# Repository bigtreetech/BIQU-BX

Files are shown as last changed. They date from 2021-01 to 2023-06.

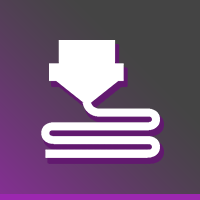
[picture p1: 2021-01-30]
Firmware/Copy to microSD to update/TFT70/bmp/print.bmp

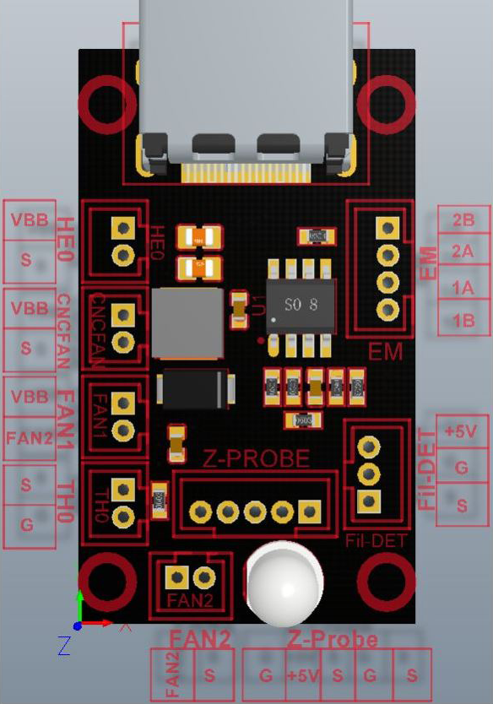
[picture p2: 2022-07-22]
Hardware/BTT BX HotMode V2.0.png

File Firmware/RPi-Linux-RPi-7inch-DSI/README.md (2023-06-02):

# RPi-7inch-DSI

## Support OS

| Hardware | 32-bit | 64-bit |
|  :---: | :---: | :---: |
|  RPi-3 | 6.1.21 |  6.1.21 |
|  RPi-4 | 6.1.21 | 6.1.21 |

## Start installation
1. Download driver from Git
    ``` bash
    git clone --depth=1 -b RPI-DSI-BXV3 https://github.com/bigtreetech/BIQU-BX.git RPI-DSI-BXV3
    ```
    
2. Install the driver
    ``` bash
    cd RPI-DSI-BXV3
    sudo ./install.sh
    ```

3. Wait for the system to restart, and then the display and touch will work normally.

> NOTE: 
> * The above steps need to ensure that the raspberry pi can be connected to the Internet normally.
> * When raspberry pi was started, the display of uboot was still 800*480 resolution, so the display was still abnormal when it was just started. The DSI output would not be normal until the system was running normally
> * Different hardware and kernel versions correspond to different drivers.

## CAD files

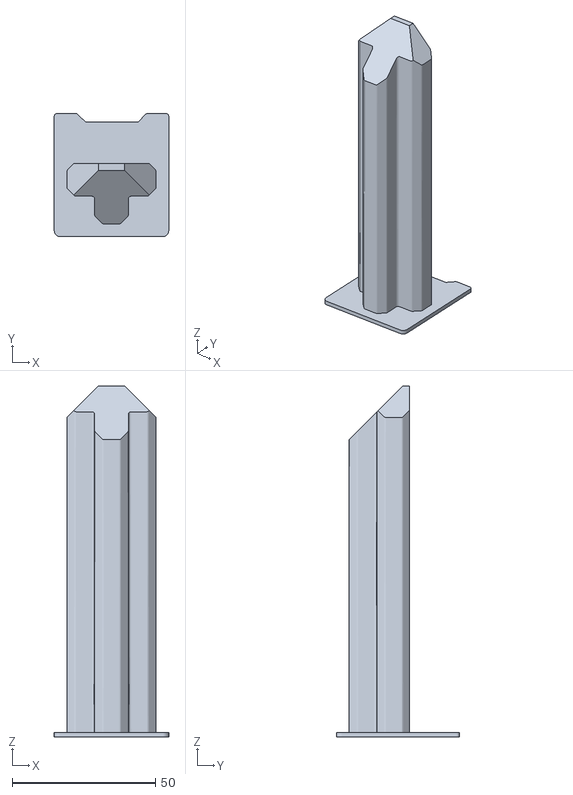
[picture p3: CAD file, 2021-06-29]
TF card data/Models/Drawer.stl
40.0 x 43.0 x 122.6

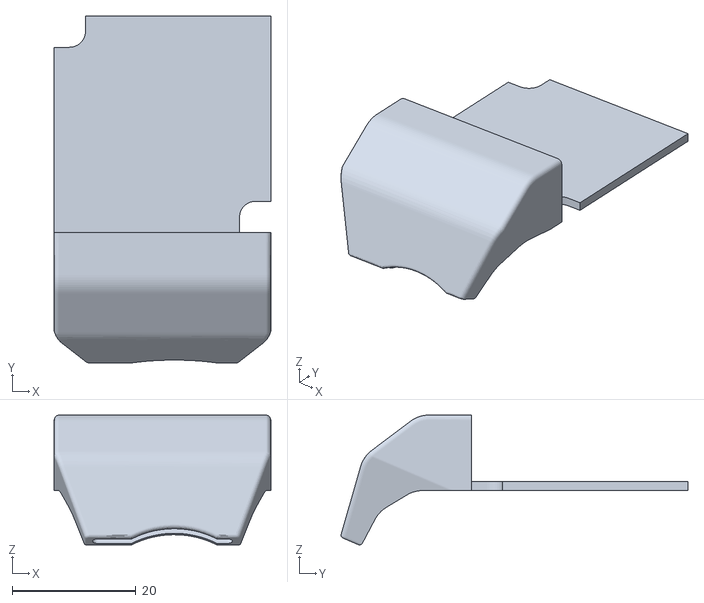
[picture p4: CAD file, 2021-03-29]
TF card data/Models/Parts-Cooling-Fan.stl
35.0 x 56.1 x 21.0

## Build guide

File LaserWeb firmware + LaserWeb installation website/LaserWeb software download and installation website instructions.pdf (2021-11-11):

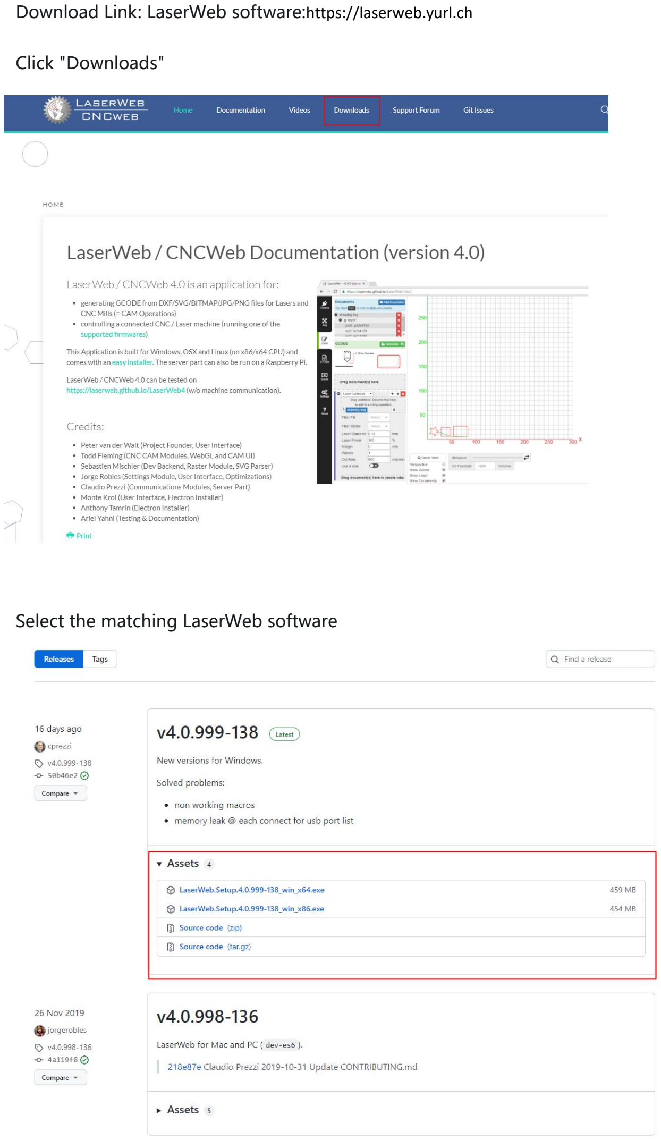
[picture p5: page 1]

Download Link: LaserWeb software:https://laserweb.yurl.ch

Click "Downloads"

Select the matching LaserWeb software

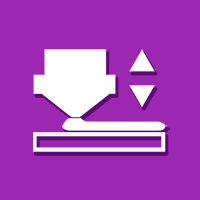
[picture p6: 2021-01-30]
Firmware/Copy to microSD to update/TFT70/bmp/BabyStep.bmp

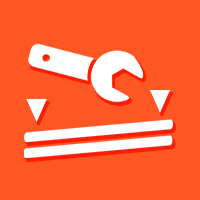
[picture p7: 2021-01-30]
Firmware/Copy to microSD to update/TFT70/bmp/manual_level.bmp

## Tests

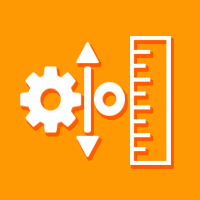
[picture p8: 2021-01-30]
Firmware/Copy to microSD to update/TFT70/bmp/tune_extruder.bmp

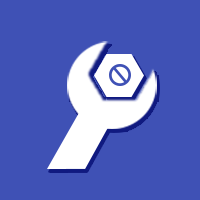
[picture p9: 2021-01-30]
Firmware/Copy to microSD to update/TFT70/bmp/tuning.bmp

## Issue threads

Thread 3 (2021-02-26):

Issues with ABL

KillerOfPie, 2021-02-26:
I just received and setup my BX yesterday and whenever I try to run the ABL it fails. The light on the sensor lights up when it approaches the sheet but the print says it fails significantly above the bed and the z endstop.

Wasn't sure if this is the proper place to report this, if not please let me know where.

KillerOfPie, 2021-02-26:
Once I removed the SD card that came with the printer the ABL worked and everything was fine after putting the card back in.

Closed 2021-02-26.

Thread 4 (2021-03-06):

Unable to Recompile Firmware

dastolly, 2021-03-06:
Cannot compile firmware with a successful flash, even without making any changes to the downloaded files.  Using VS.  I'm trying to get the USB on the TFT to be the connection to Octoprint, as well as enable safe home, but I cannot make these changes and have the printer successfully load the new firmware.  It runs the process up to 100%, but never boots, just stays at a black screen.

inismor, 2021-03-09:
> Cannot compile firmware with a successful flash, even without making any changes to the downloaded files. Using VS. I'm trying to get the USB on the TFT to be the connection to Octoprint, as well as enable safe home, but I cannot make these changes and have the printer successfully load the new firmware. It runs the process up to 100%, but never boots, just stays at a black screen.

Are you compiling BTT_SKR_SE_BX_BOOT? (Not BTT_SKR_SE_BX). Worked for me.

dastolly, 2021-03-11:
> > Cannot compile firmware with a successful flash, even without making any changes to the downloaded files. Using VS. I'm trying to get the USB on the TFT to be the connection to Octoprint, as well as enable safe home, but I cannot make these changes and have the printer successfully load the new firmware. It runs the process up to 100%, but never boots, just stays at a black screen.
>
> Are you compiling BTT_SKR_SE_BX_BOOT? (Not BTT_SKR_SE_BX). Worked for me.

I'm compiling in Visual Studio and I can open 3 folders from the downloaded code.  One folder says "BIQU-BX", one says "BIQU-BX-1", and one says "BIQU-BX-master".  All three folders have similar innards, and all reside inside a "BIQU-BX-master" folder.  No matter which one I select, when I build, the marline auto build shows BTT_SKR_SE_BX.  How can I get to the boot one?

inismor, 2021-03-11:
What you describe isn’t what I saw, and I just downloaded the sources a couple of days ago. PlatformIO only shows BTT_SKR_SE_BX and BTT_SKR_SE_BX_BOOT. Build the _BOOT version and copy the resulting firmware.bin file to an SD card. First time you flash the printer, be sure to add the “config.ini" file and “BTT70" folder from the top-level "Copy to microSD to update” folder. BTT has made some changes to the UI since they shipped.

—r

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

dastolly, 2021-03-11:
> What you describe isn’t what I saw, and I just downloaded the sources a couple of days ago. PlatformIO only shows BTT_SKR_SE_BX and BTT_SKR_SE_BX_BOOT. Build the _BOOT version and copy the resulting firmware.bin file to an SD card. First time you flash the printer, be sure to add the “config.ini" file and “BTT70" folder from the top-level "Copy to microSD to update” folder. BTT has made some changes to the UI since they shipped. —r
> […](#)
> On Mar 10, 2021, 7:20 PM -0500, dastolly ***@***.***>, wrote: > > Cannot compile firmware with a successful flash, even without making any changes to the downloaded files. Using VS. I'm trying to get the USB on the TFT to be the connection to Octoprint, as well as enable safe home, but I cannot make these changes and have the printer successfully load the new firmware. It runs the process up to 100%, but never boots, just stays at a black screen. > Are you compiling BTT_SKR_SE_BX_BOOT? (Not BTT_SKR_SE_BX). Worked for me. I'm compiling in Visual Studio and I can open 3 folders from the downloaded code. One folder says "BIQU-BX", one says "BIQU-BX-1", and one says "BIQU-BX-master". All three folders have similar innards, and all reside inside a "BIQU-BX-master" folder. No matter which one I select, when I build, the marline auto build shows BTT_SKR_SE_BX. How can I get to the boot one? — You are receiving this because you commented. Reply to this email directly, view it on GitHub, or unsubscribe.

I'll give it a shot again, thanks!  I'm just not seeing where to choose between the two.  I'll keep digging.

inismor, 2021-03-11:
You build with PlatformIO, right? Not the compile button.

dastolly, 2021-03-11:
In Visual?  I've been using auto build marlin... I'm in it now, trying to find it.  Thanks for sticking with me.

inismor, 2021-03-11:
Yeah, you have to use PlatformIO. It ensures that the proper libraries are present and linked into the code. The PlatformIO plug-in for VSCode is free.

—r

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

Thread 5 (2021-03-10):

SD card files

jtatum, 2021-03-10:
Is there a download somewhere that has all the SD card files? My SD card arrived blank/corrupted.

Will-wastelander, 2021-03-10:
I have been requesting this for a few weeks now.

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

looxonline, 2021-03-20:
There are links to it on their facebook group.

predy3dprint, 2021-03-20:
But not everybody has a Facebook Account :-(

thisiskeithb, 2021-03-20:
They’ve been uploaded: https://github.com/bigtreetech/BIQU-BX/tree/master/TF%20card%20data

thisiskeithb, 2021-03-22:
Here's a PR to add the original parts cooling duct STL: https://github.com/bigtreetech/BIQU-BX/pull/6

TRIBVNE, 2021-04-10:
> Is there a download somewhere that has all the SD card files? My SD card arrived blank/corrupted.

When you say "blank/corrupted" are you getting a read error?  I am getting a read error no matter what I try, and the only adapter I have to check it on my computer is the poor quality one that came with the BX.  It won't be recognized by my computer even if I try it with a card I have full of photos.

thisiskeithb, 2021-06-08:
https://github.com/bigtreetech/BIQU-BX/pull/13 adds the missing STL for the drawer.

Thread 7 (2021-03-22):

Using cura profile

grimlokason, 2021-03-22:
Hello,

There is a cura profile to load, but no instruction on which printer we must use as a base.
Is it possible to add that instruction  ?

NB : with loading on a BIQU B1 in cura 4.8.0 we got an error :
```Failed to import profile from C:/Users/grim_lokason/Downloads/BIQU-BX configuration file(1).curaprofile: Quality type 'normal' is not compatible with the current active machine definition 'biqu_base'.```

Best regards.

thisiskeithb, 2021-03-22:
Using Cura 4.8?

Will-wastelander, 2021-03-22:
I have tried with Cura 4.6, 4.7, and 4.8 and get an error when attempting
to the supplied profile.

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

looxonline, 2021-03-23:
> after more digging, the biqu_base.def.json is installed but not detected in the printer list in cura :/

The base definition is not a printer. It is a collection of settings that form a base for all BIQU machines to build off. A Cura profile is in development but since there has been no Cura release since Q3 2020 there has been no opportunity to have it integrated into upstream cura. If you would like to trial it and provide feedback you are more than welcome to do so by following the guide here: https://www.facebook.com/groups/1012996125813700/permalink/1156048964841748

hoyohayo, 2021-07-21:
Is there any way of being able to take part in the trial without having to use facebook?

I actually do not own an account, but would still like to participate and give feedback on that.

thisiskeithb, 2021-07-21:
> Is there any way of being able to take part in the trial without having to use facebook?

https://github.com/Ultimaker/Cura/pull/10086 was merged, so there will be a profile for the BX in Cura 4.11.

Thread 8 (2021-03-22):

Marlin configuration ?

grimlokason, 2021-03-22:
Hello,

There is a marlin folder on this projet, but i'm not able to find the config files for the biqu BX.

Is it possible to add them ?

There is the necessary for the B1 : https://github.com/MarlinFirmware/Configurations/tree/import-2.0.x/config/examples/BIQU

Best regards.

thisiskeithb, 2021-03-22:
This printer is not supported upstream.

You’ll need to use the firmware from this repo as-is until it’s merged upstream and I’ll have a BX config ready similar to what I did for the B1.

grimlokason, 2021-03-23:
In fact, i was hopping too take a look at some conf information since i've a biqu H2 (the same extruder as in the BX if i'm right ),  on a ender 3v2 and didn't have great result.

If we take a look here : https://damsteen.nl/blog/2021/01/19/mounting-the-biqu-h2-to-creality-cr6 on "Other advanced settings"
He say to modify RETRACT_LENGTH / PAUSE_PARK_RETRACT_LENGTH / FILAMENT_CHANGE_UNLOAD_FEEDRATE / FILAMENT_CHANGE_UNLOAD_LENGTH / FILAMENT_CHANGE_FAST_LOAD_FEEDRATE  but i don't know how he choose those information :/

thisiskeithb, 2021-03-23:
> He say to modify RETRACT_LENGTH / PAUSE_PARK_RETRACT_LENGTH / FILAMENT_CHANGE_UNLOAD_FEEDRATE / FILAMENT_CHANGE_UNLOAD_LENGTH / FILAMENT_CHANGE_FAST_LOAD_FEEDRATE but i don't know how he choose those information :/

You can find that information in the BX config located in this repo: https://github.com/bigtreetech/BIQU-BX/blob/ce7c484c01f9e4bb9f87592a8fb6a1d4d184f583/Firmware/Marlin-2.0.6-BX/Marlin/Configuration_adv.h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

grimlokason, 2021-03-23:
Thank you !
I don't know why i haven't been able to found it in the project.

Closed 2021-03-23.

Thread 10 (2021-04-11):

Model gcode files

Protocol-X, 2021-04-11:
All of the models appear to be in a hex type format.   Please provide the correctformat.   You have provided us start and end code to set up these printers and there is no way to extract it from these files.  Trying to convert them to ascii just results in gibberish.

thisiskeithb, 2021-04-11:
The `.gcode` files have image preview data embedded so you have to scroll below that.

Example: For the current [3DBenchy.gcode](https://github.com/bigtreetech/BIQU-BX/blob/5c7d32e474446e1a88884869bf2cec28986cf9e2/TF%20card%20data/Models/3DBenchy.gcode), the Simplify3D gcode starts around 593:

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

Protocol-X, 2021-04-11:
Thank you for the information Keith

On Sun, Apr 11, 2021, 1:51 PM Keith Bennett ***@***.***>
wrote:

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

Protocol-X, 2021-07-26:
User error.

Closed 2021-07-26.

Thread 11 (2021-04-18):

Printer reboots during abl

Protocol-X, 2021-04-18:
This issue didn't exist on the original firmware,  but with this version, if you try to adjust the z offset while auto level,  the pinter reboots.

jannoke, 2021-07-26:
This exists in original firmware also. I just got mine and factory spec firmware reboots also. Mine was built jan 2021

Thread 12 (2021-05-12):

Settings are not permanently saved to EEPROM

inferior-minion, 2021-05-12:
Whenever any new settings (such as new PID settings, Z offset, etc.) are saved they are lost after powering off the printer.

inferior-minion, 2021-05-12:
I have compiled the latest firmware on GitHub and tested on both the current compiled version and the version I compiled (screen flash fix) and confirmed this issue is present in both firmware versions.

Dalthoraz, 2022-07-17:
Has any progress been made on this I have the same problem over a year later with a new printer.

Rick18101965, 2022-07-17:
Nope.  I have another one in box and will see if new card in machine will
mak a difference otherwise the advice is to update main board by ethernet
tp comp....a royal pain..

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

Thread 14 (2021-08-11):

Marlin-2.0.6-BX compiled firmware.bin results in black screen for TFT

R60D, 2021-08-11:
I was trying to flash my BIQU-BX with the latest compiled version using VSCODE AUTO BUILD MARLIN
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

Video of bricked BIQU-BX
https://user-images.githubusercontent.com/29761720/129068880-8d21c268-b605-46c7-90f6-5004df94bf8b.mP4

I was able to use the printer by flashing the pre-compiled firmware.bin that comes with the TFT icons, but I still cannot compile my own firmware.bin

R60D, 2021-08-12:
So I did some digging and found a repo that works for the BIQU-BX.

https://github.com/looxonline/Marlin/tree/BIQUBX_ALMOST_STOCK

I compiled the BTT_SKR_SE_BX_BOOT Enviroment. After flashing it to my printer, it worked like a charm. I had to remove the physical Z-endstop though as it is explained in the repo.
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

Gwebber-Net, 2022-01-07:
I have the same issue, can a developer answer ?

Mrjeanswe, 2022-05-10:
same problem , any solutions?

Gwebber-Net, 2022-05-10:
There is this firmware.
Go to the biqu bx Facebook page.     And look for the get started section.

You will find a GitHub page , with firmware for the stock machine

Outlook voor Android<https://aka.ms/AAb9ysg> downloaden
________________________________
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

Rick18101965, 2022-05-10:
Not as yet thar i have heard...

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

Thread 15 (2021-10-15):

Head crashing on homing Z

exxosuk, 2021-10-15:
I found part of this the problem with the Z- switch being unreliable. I have since changed it for a Hall effect switch which has greatly improved part of the problem.

However, there seems to be some scenarios where the Z axis is already homed, and when you manually home with G28, the head will continue to move towards the bed bending the mechanism upwards!

This does not always seem to happen. But there needs to be something in the software where homing the axis always moves Z axis upwards by something like 2mm first. Currently if it is already in the home position, and you home, it moves downwards crashing into the bed.

Currently homing seems to move the head downwards until switch is pressed. Its fair enough, but if the switch is already pressed it continues to move downwards causes the bed crash issue. Then the head will move upwards and slowly moved down again this time it will home correctly. Trying to manually move the z-axis downwards results in no movement as expected.

So there is clearly something wrong with the firmware. The homing Z axis should always move upwards until the switches released. Not move downwards straight away because if the switch is already closed it will cause the bed crash.

Redam-Desiagn, 2022-01-14:
I found that adjusting the Z-switch a bit to get nozzle not crashing into bed helps but this is quite fiddly to get right.

Closed 2022-02-18.

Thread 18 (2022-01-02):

Too long extrusion prevented, when printing more then 1 model

Gwebber-Net, 2022-01-02:
When i am printing more then 1 model, always after a couple of layers, the error message pops up,
"Too long extrusion prevented".

And the most funny thing,
After that error, for some weird reason, my printer starts to print, an entirely different model, ontop of what is already printed.
So i was printing a Steppermount, and a benchy was printing halfway through.

radek8, 2022-01-04:
try to increase the value
#define EXTRUDE_MAXLENGTH

Gwebber-Net, 2022-01-05:
Yes, I figured that would help,. But I wasnt interested inin going into the firmware for a brand new printer.

I try to not tinker with it.

Outlook voor Android<https://aka.ms/AAb9ysg> downloaden
________________________________
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

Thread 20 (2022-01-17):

Axis endstop problem

exxosuk, 2022-01-17:
it seems the BX does not actually have physical end stop switches. I'm not sure how it is actually detecting the end stop, assume it is when the motor starts pulling more current or something ?

In any case, even if the belts are relatively tight, the homing on X&Y fails to function. For my X-axis it never fully reaches the far left. And for the Y-axis it pretty much does not move at all. But if I very gently press the bed backwards as it tries to move it homes correctly. The only way it can work is if the belts are extremely loose which is not good as it causes other problems.

I tried upping the motor current but that does not seem to change anything.

So how to fix it ?

exxosuk, 2022-01-17:
hmmm

https://marlinfw.org/docs/gcode/M914.html

Closed 2022-01-17.

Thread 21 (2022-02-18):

Y-axis moves fine but cannot home

exxosuk, 2022-02-18:
When I manually move the bed with the Y+- buttons it moves fine. But when I home Y-it sounds like the motors are stalling as it cannot move ?

I have tried adjusting the bump sensitivity but the bed even moves a tiny bit tour just sits there growling like the motors do not have enough power to move the bed.

So is there a separate amperage set to the motors when homing as opposed to when manually moving the axis ?

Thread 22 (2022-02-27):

Random restarts

AndyUK300ZX, 2022-02-27:
Is anyone experiencing random restarts after printer has been printing for over an hour?

Having finally got my BX printing well, any model that requires long print times fail. I've printed the usual files that came on the SD Card but once I started to print other files everything started going wrong.

None of the gcode files I create in Ultimaker Cura will complete a print. After an hour or so the print powers off then reboots. No print resume option even though print resume is on.

Is this a faulty machine or something in the code? I've used several different SD Card or USB stick all connected to the USB port on the TFT

petrbraha, 2022-02-27:
I have same issue, random restarts when printing from USB or SD card connected to TFT. When I print from microSD card connected to mainboard, it prints ok.

AndyUK300ZX, 2022-02-27:
> I have same issue, random restarts when printing from USB or SD card connected to TFT. When I print from microSD card connected to mainboard, it prints ok. Same G-Code at USB, SD and microSD.

That's helpful to know, thanks. Guess there must be an issue with the data pass through from the TFT.

Will test tomorrow to see if mine will work OK from the main board

Drue74, 2022-08-10:
Anyone nail this down yet? Just got printer an it's doing that.

Rick18101965, 2022-08-11:
Nope but going to look this weekend if i have time.  I will look at bq
advising i update firmware.  Got the laptop and wire now and not looking
forward to it.  Pity not ok out of the box.

Rick

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

Taz21017, 2022-10-01:
I have returned two machines that did exactly what was described. Did updating the firmware correct the issue?

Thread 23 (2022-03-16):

Long filenames refuse to start printing

qkdefus, 2022-03-16:
I have an issue where i use a Cura plugin that let me auto re-name sliced files using prefix

[year]_[abbr_machine]_[print_time_hours]h[print_time_minutes]m_[material]_[layer_height]mm_[speed_print]mms_[object_count]x_-_[base_name]_-_[scale]%scale

this results in ofcourse long filenames where my ender 3 pro and ender 2 pro does not have any issue with, both running close to if not latest marlin and octoprint.
however my new biqu bx printer refuse to start printing files with long filenames.

qkdefus, 2022-03-16:
renaming the files with shorter name will print the file just fine.

radek8, 2022-04-17:
In Marlin, enable support for long file names and then compile a new FW.

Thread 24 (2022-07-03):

Probing Failed

kenswain, 2022-07-03:
After bed heats up once the move ment starts to start probing machine returns erorr : probing failed

aka1ceman, 2023-05-18:
I have SAME issue

johnp789, 2023-06-04:
My BIQU BX printer had progressively more frequent ABL probing failures until it could not ever complete a 25-point grid.  Today, I replaced the HDMI cable with another generic HDMI cable, and I have completed 3 full 25-point ABL grids since with no ABL probing failures.  Replacing the HDMI cable is not too difficult---I took the bottom rear panel off to access the port on the controller board.

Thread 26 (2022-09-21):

Using the BX TFT70 withouth the SKR SE BX board

aodxxl, 2022-09-21:
Good day.
I have raised the issue many times on facebook but nobody seems to know exactly if it is possible.
My SKR SE BX board has gived me the magic smoke during  printing. I was using the board in a voron-like printer alongside a second MCU for controlling Z steppers. I  purchased the Manta M8P with plans on using it instead of the SKR and second MCU. I want to reuse the BX screen with the new Manta board through HDMI.

Luke managed to make it work by providing 5V to the board via ground and a Mosfet plus shorting out 2 pins on the LCD connector.
Unfortunately Luke is using an older version of the BX screen board and on the newer V2.2 boards, that mosfet is missing and the mod doesn not work even after discovering a way to power on the board. Shorting pin 1 and 14 does nothing( as per Luke's mod)

The issue:
When giving 5V to pin 1 and gnd to pin 2 on the LCD connector, the screen backlight and backside LEDS turn on but there is no image displayed on the screen. When using the wheel/selector( marlin/pi/legacy) it does nothing.
The HDMI board on the back of the screen has the HDMI Chip needed to display an image from a source and it looks like all the power connections are there so that means that the SKR BX SE board just gives video signal to the screen. There has to be an enable pin that enables the screen and its functions.

Please Bigtreetech, help me not create e-waste so i can recycle the screen with one of your shiny new boards :) And also you are a company that enables tinkerers , ENABLE ME :D or my screen at least :)

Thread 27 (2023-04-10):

Problems with the "pause" command BIQU BX

WFloripes, 2023-04-10:
Hello, I'm experiencing a problem with the "pause" command, both via the slicer and via the touchscreen.
The pause is made normally, but on the return, the nozzle is displaced by 0.9mm from the last point. The offset is only on the Y axis.
I tried to change the firmware (BIQU BX Master) but the problem remains.
I would like to change the firmware, but I can't do it in VS Code, for some reason.
Any thoughts on the pause issue? Thanks.

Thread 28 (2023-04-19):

CB1 Integration

kasuke5, 2023-04-19:
Since RPI are a pain in the ass to get but not a CB1 that is also a BTT product, it would be nice to have a special configuration, because it's not as easy and the same than with a RPI.
A guide and configuration for Ocotprint and Klipper would be great.
I personnaly stay with octoprint with my CB1 but need some extra config.

varazir, 2023-08-10:
CB1 do not work with the BX v3 as  CB1 do not support DSI :(

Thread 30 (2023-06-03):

BX with V3 screen and controller board with new drivers

varazir, 2023-06-03:
I found out yesterday that a new driver for the SDI screen is out.
Happily installed it on my RPi 3b+, I got Klipper screen to show correct resolution  but with the terminal was bleeding thru.
The touchscreen on  was a bit off, need to calibrate that.

When I rebooted  again it stopped working,

I'm seeing this in dmesg is

```
[    9.055692] bcm2835-isp bcm2835-isp: Loaded V4L2 bcm2835-isp
[    9.058314] bcm2835-codec bcm2835-codec: Device registered as /dev/video10
[    9.058370] bcm2835-codec bcm2835-codec: Loaded V4L2 decode
[    9.075144] bcm2835-codec bcm2835-codec: Device registered as /dev/video11
[    9.075203] bcm2835-codec bcm2835-codec: Loaded V4L2 encode
[    9.082463] bcm2835-codec bcm2835-codec: Device registered as /dev/video12
[    9.082537] bcm2835-codec bcm2835-codec: Loaded V4L2 isp
[    9.088201] bcm2835-codec bcm2835-codec: Device registered as /dev/video18
[    9.088260] bcm2835-codec bcm2835-codec: Loaded V4L2 image_fx
[    9.093321] bcm2835-codec bcm2835-codec: Device registered as /dev/video31
[    9.093379] bcm2835-codec bcm2835-codec: Loaded V4L2 encode_image
[    9.172640] snd_bcm2835: module is from the staging directory, the quality is unknown, you have been warned.
[    9.177966] bcm2835_audio bcm2835_audio: card created with 8 channels
[    9.370676] i2c i2c-11: Added multiplexed i2c bus 0
[    9.374136] i2c i2c-11: Added multiplexed i2c bus 10
[    9.437585] input: raspberrypi-ts as /devices/platform/soc/soc:firmware/soc:firmware:touchscreen/input/input0
[    9.918106] cfg80211: Loading compiled-in X.509 certificates for regulatory database
[   10.079450] cfg80211: Loaded X.509 cert 'sforshee: 00b28ddf47aef9cea7'
[   10.100017] cfg80211: loaded regulatory.db is malformed or signature is missing/invalid
[   10.253682] brcmfmac: F1 signature read @0x18000000=0x15264345
[   10.271051] brcmfmac: brcmf_fw_alloc_request: using brcm/brcmfmac43455-sdio for chip BCM4345/6
[   10.272059] usbcore: registered new interface driver brcmfmac
[   10.580572] brcmfmac: brcmf_c_preinit_dcmds: Firmware: BCM4345/6 wl0: Nov  1 2021 00:37:25 version 7.45.241 (1a2f2fa CY) FWID 01-703fd60
[   11.447907] rpi_touchscreen_attiny 10-0045: Unknown Atmel firmware revision: 0x11
[   12.183535] Adding 262140k swap on /var/swap.  Priority:-2 extents:2 across:2129916k SSFS
[   12.207049] 8021q: 802.1Q VLAN Support v1.8
[   12.475902] brcmfmac: brcmf_cfg80211_set_power_mgmt: power save disabled
```

My config.txt file
https://gist.github.com/varazir/7f58c43baf82cafdb4d9e42482428b85

Screenshot when it was working
https://i.imgur.com/RkRlVwX.png

varazir, 2023-06-04:
Klipperscreen is showing now after I used a new config.txt file.

varazir, 2023-06-04:
Added disable_splash=1 and now I don't have any bleeding thru.
The touchscreenarea is fine now as well.

Closed 2023-06-04.

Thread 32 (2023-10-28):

Update the script/drivers  RPI-DSI-BXV3

varazir, 2023-10-28:
There a new kernel and the script fails.

bendermh, 2024-01-12:
Until Biqu does not fix this you can use/flash "legacy 32/64 bit" raspian version in your pi 4 board.

varazir, 2024-01-12:
I found a solution, created a GIST.

varazir, 2024-01-12:
> Until Biqu does not fix this you can use/flash "legacy 32/64 bit" raspian version in your pi 4 board.

I found the correct image and updated my guide on gist.

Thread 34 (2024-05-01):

Newest Marlin with Graphical UI

gibawatts, 2024-05-01:
HI,

I am new to firmware compilation and need some help. I managed to compile the latest bugfix version of Marlin and it worked. I have the Marlin Interface and need to know how to add the Graphical UI and Raspiberry PI options like in the stock firmware.

Regards

thisiskeithb, 2024-06-01:
BTT never ported their UI upstream to Marlin, so it's not included. There's no display mode switching either.

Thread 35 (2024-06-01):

BX now shipping with single Z driver & PT100/PT1000 with MAX31865?

thisiskeithb, 2024-06-01:
In https://github.com/bigtreetech/BIQU-BX/commit/475c6b5c8923bfd69c9bd2a1bae81f4b93301507, the config was changed to use a single Z driver &  PT100/PT1000 with MAX31865.

Examples:

https://github.com/bigtreetech/BIQU-BX/blob/475c6b5c8923bfd69c9bd2a1bae81f4b93301507/Firmware/Marlin-2.0.6-BX/Marlin/Configuration.h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

https://github.com/bigtreetech/BIQU-BX/blob/475c6b5c8923bfd69c9bd2a1bae81f4b93301507/Firmware/Marlin-2.0.6-BX/Marlin/Configuration.h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

https://github.com/bigtreetech/BIQU-BX/blob/475c6b5c8923bfd69c9bd2a1bae81f4b93301507/Firmware/Marlin-2.0.6-BX/Marlin/Configuration.h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

https://github.com/bigtreetech/BIQU-BX/blob/475c6b5c8923bfd69c9bd2a1bae81f4b93301507/Firmware/Marlin-2.0.6-BX/Marlin/Configuration_adv.h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

Was this accidental or does the BX now ship in this configuration?

We (Marlin) still [maintain a BX config with V2 & V3 boards, dual Z, standard thermistor, etc. upstream](https://github.com/MarlinFirmware/Configurations/tree/bugfix-2.1.x/config/examples/BIQU/BX) and I can confirm that it works fine on my BX with V2 motherboard & TFT.

Sir-Charles, 2024-09-12:
I think this was just a test config for the H2V2-500C extruder. You can see they use the BX motherboard as an example in the 500C's user manual [https://cdn.shopify.com/s/files/1/1619/4791/files/4050000035-H2_500_user_manual.pdf?v=1679589018](url)

BTW does that Marlin bugfix-2.1.x config keep the TFT's multi-mode functionality (Marlin/Touch/Pi)? I just got a new BX with the SKR-BX-SE V2.0 motherboard and TFT70-V2.2, so I'm looking at updating it's old FW. I've already found loox's Marlin build but its for 2.0.6.1 still, and I've read that others have gotten 2.1.1 working but they're stuck with only Marlin mode for the TFT. If that's the case then I might just go to Klipper, seems the TFT70 can be made to work with that.

In the Info screen it says it shipped with:
System: Marlin 2.0.6.1-BX (March 19 2021 10:07:47)
Board: BIGTREETECH_TFT70_V3.0 (Back of the screen says V2.2? with the HDMI adapter, not DSI interface)
Firmware: TFT70_V3.0.SOFTWARE_VERSION Mar 19 2021

Closed 2025-06-21.

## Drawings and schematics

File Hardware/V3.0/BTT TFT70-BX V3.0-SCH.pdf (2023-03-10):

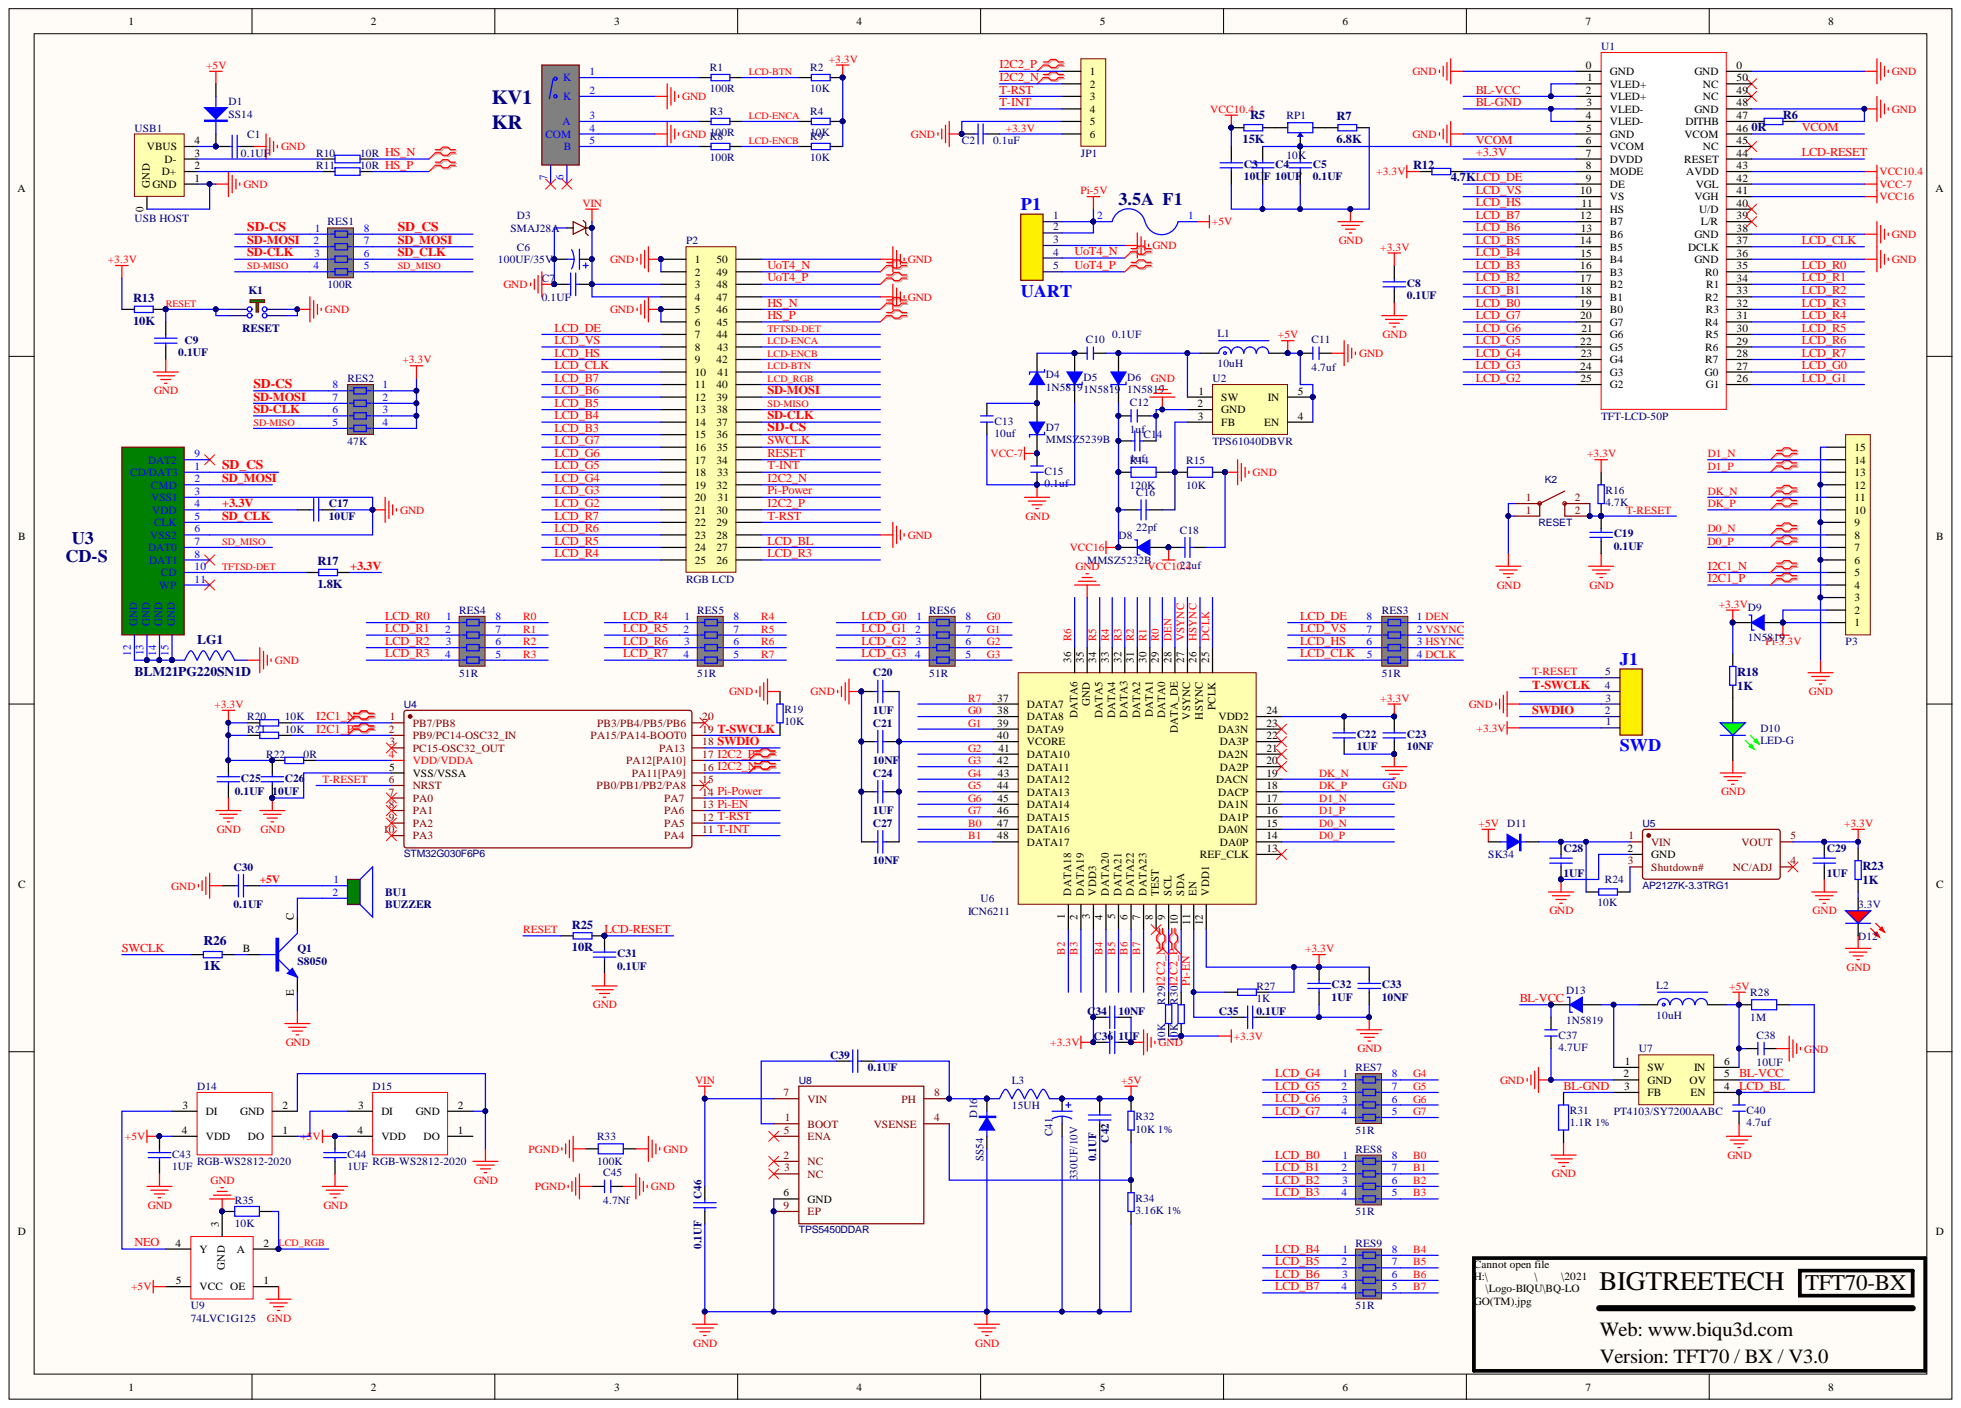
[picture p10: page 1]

SD-CS SD-MOSI

3 | LCD_B4 | SD-CLK | D7 C15

VDD1 12 REF_CLK 13 DA0P 14 DA0N 15 DA1P 16 DA1N 17 DACP 18 DACN 19 DA2P 20 DA2N 21 DA3P 22 DA3N 23 VDD2 24 PCLK 25 HSYNC 26 VSYNC 27 DATA_DE 28 DATA0 29 DATA1 30 DATA2 31 DATA3 32 DATA4 33 DATA5 34 GND 35 DATA6 36

C28 | | GND 2

Cannot open file
\Logo-BIQU\BQ-LO
GO(TM).jpg

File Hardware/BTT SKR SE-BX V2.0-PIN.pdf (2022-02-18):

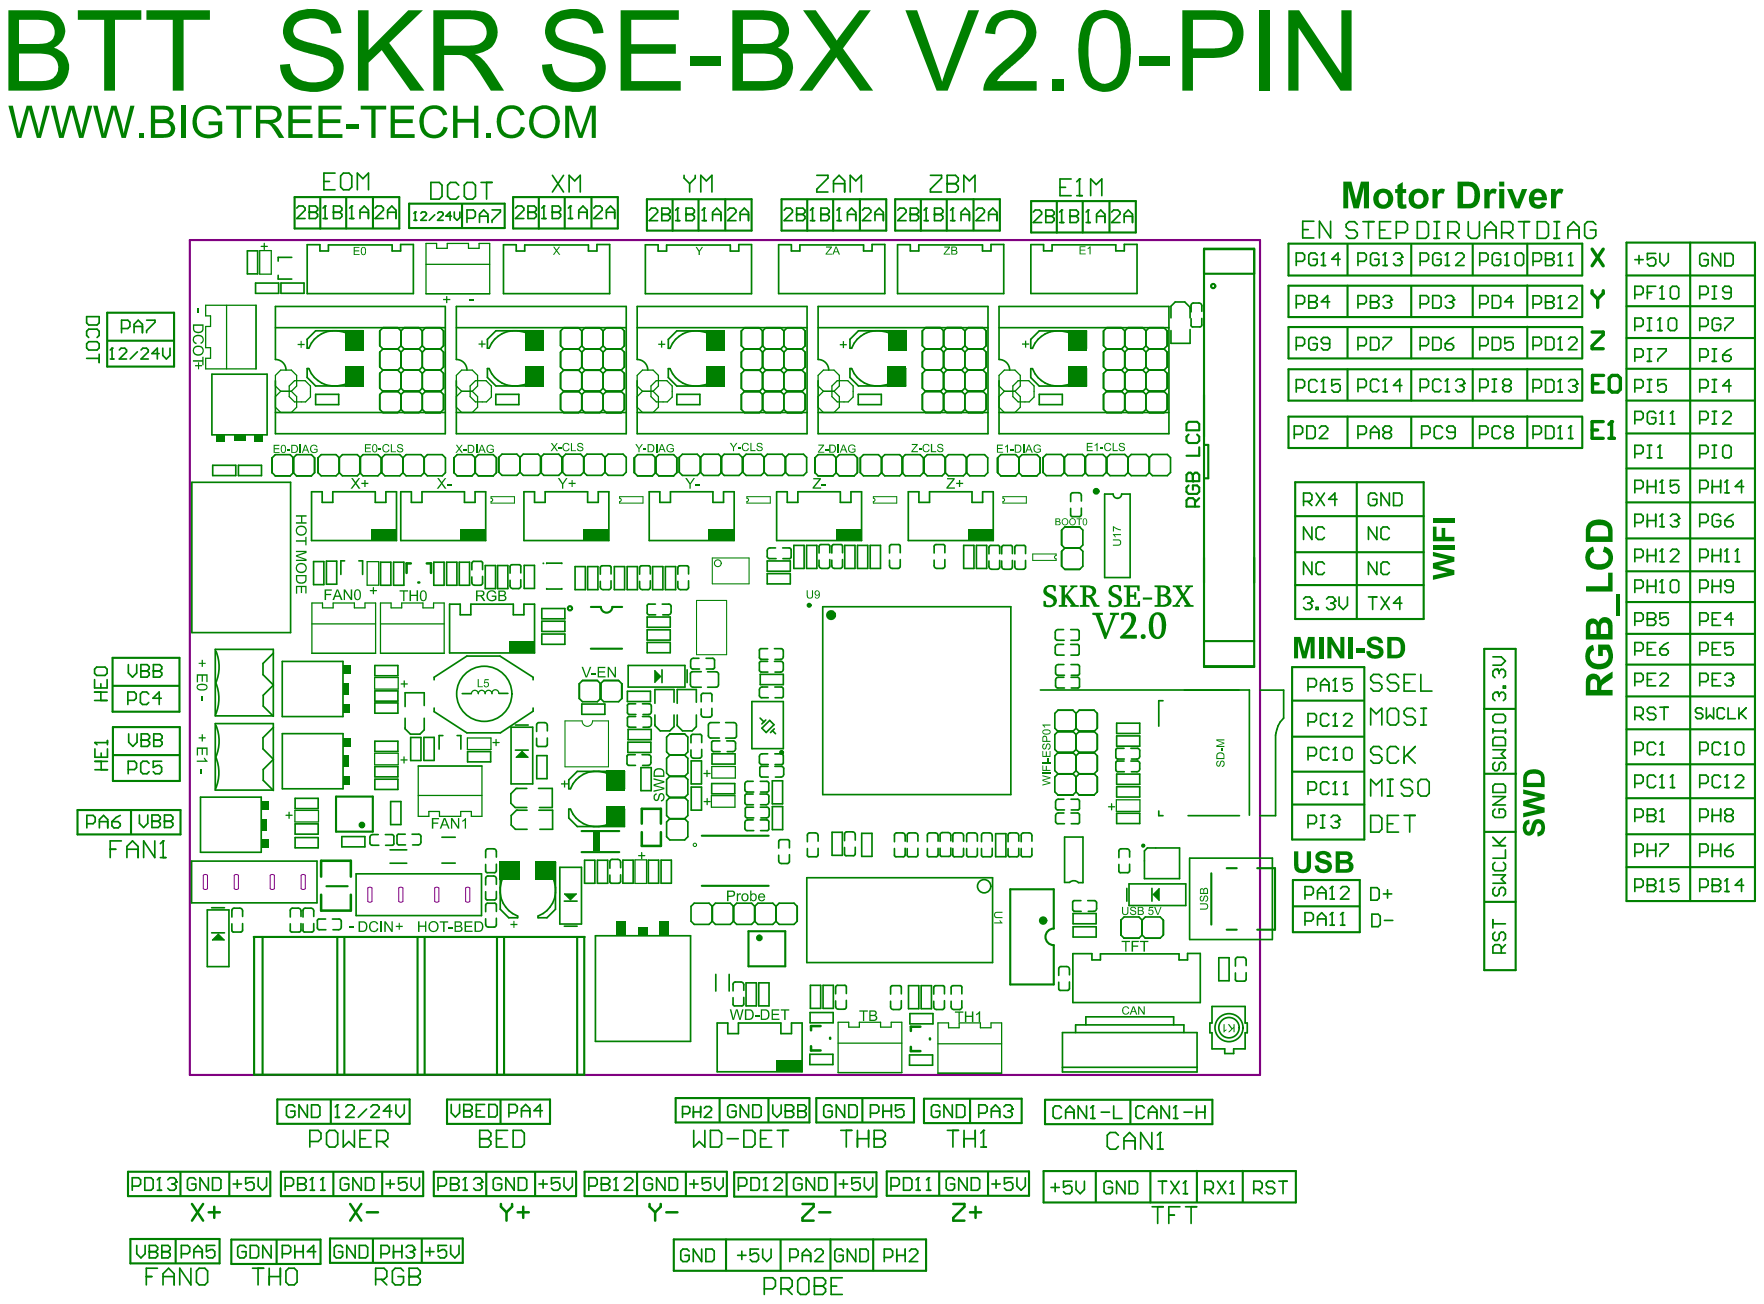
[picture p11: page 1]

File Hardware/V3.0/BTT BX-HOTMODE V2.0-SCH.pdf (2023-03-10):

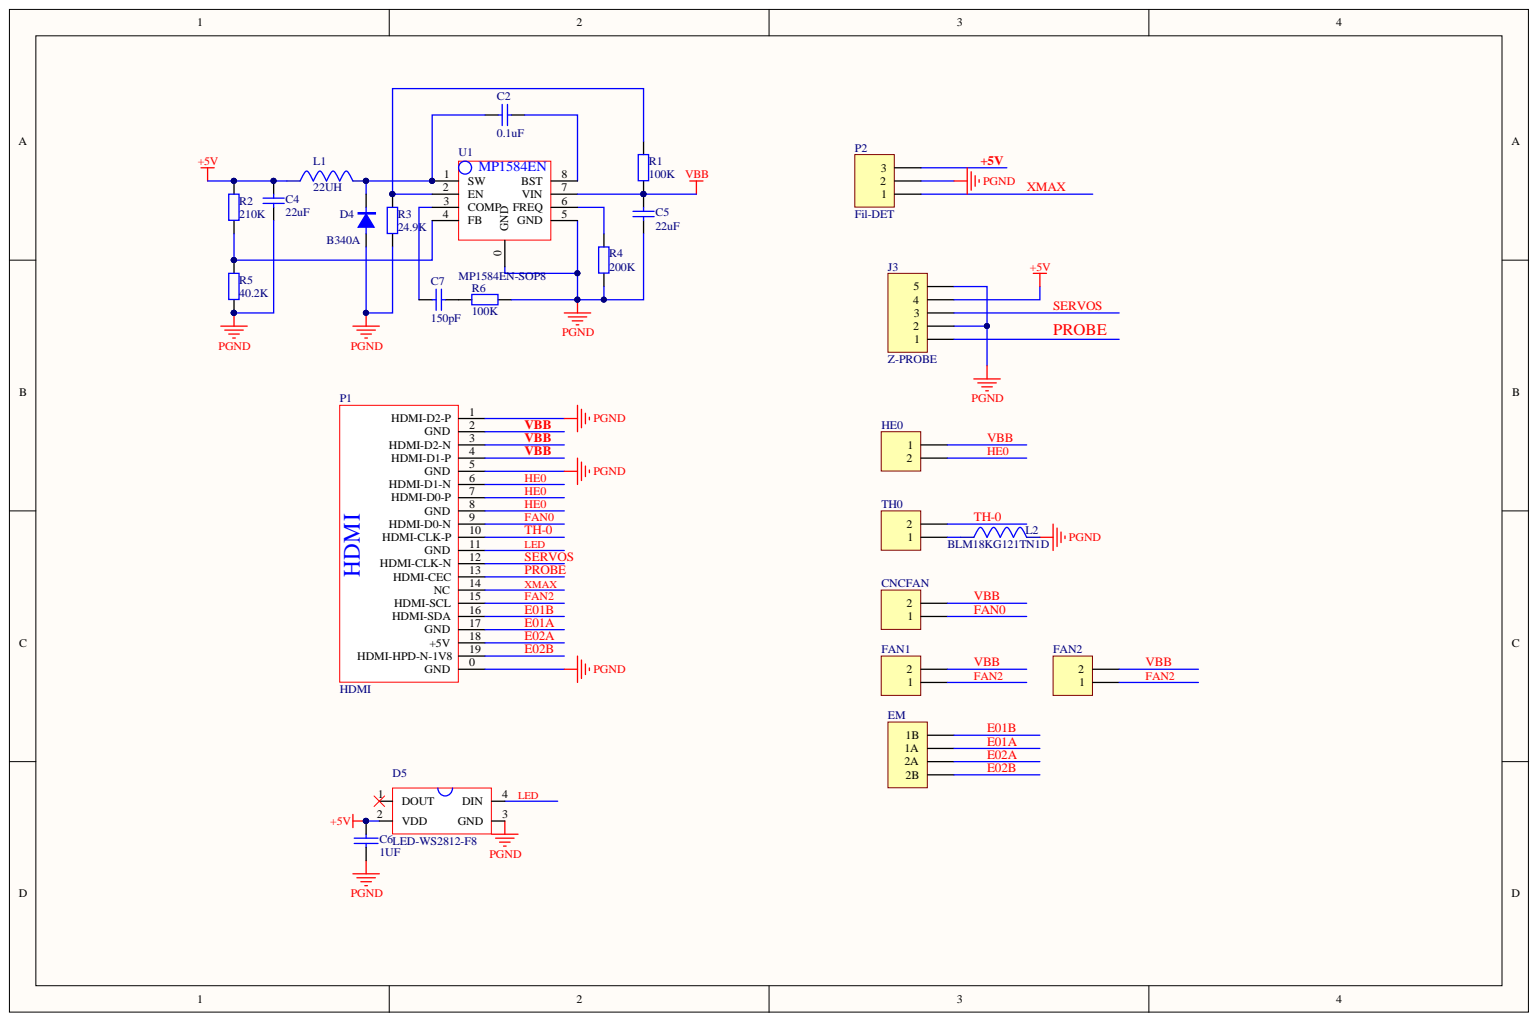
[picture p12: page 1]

COMP 3

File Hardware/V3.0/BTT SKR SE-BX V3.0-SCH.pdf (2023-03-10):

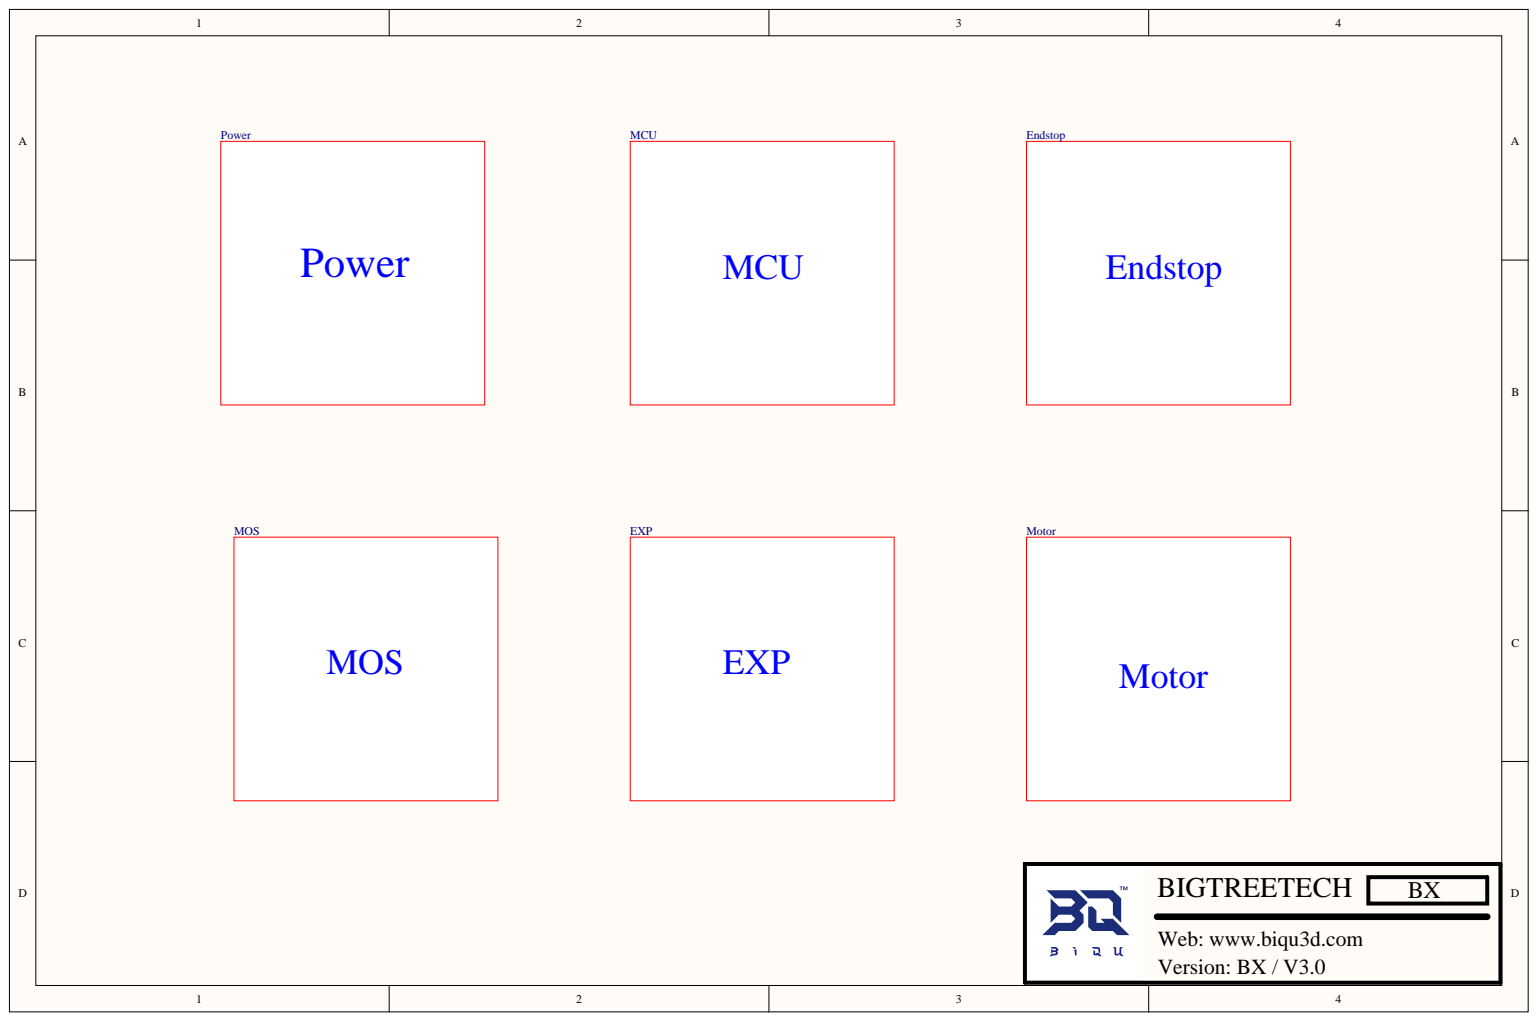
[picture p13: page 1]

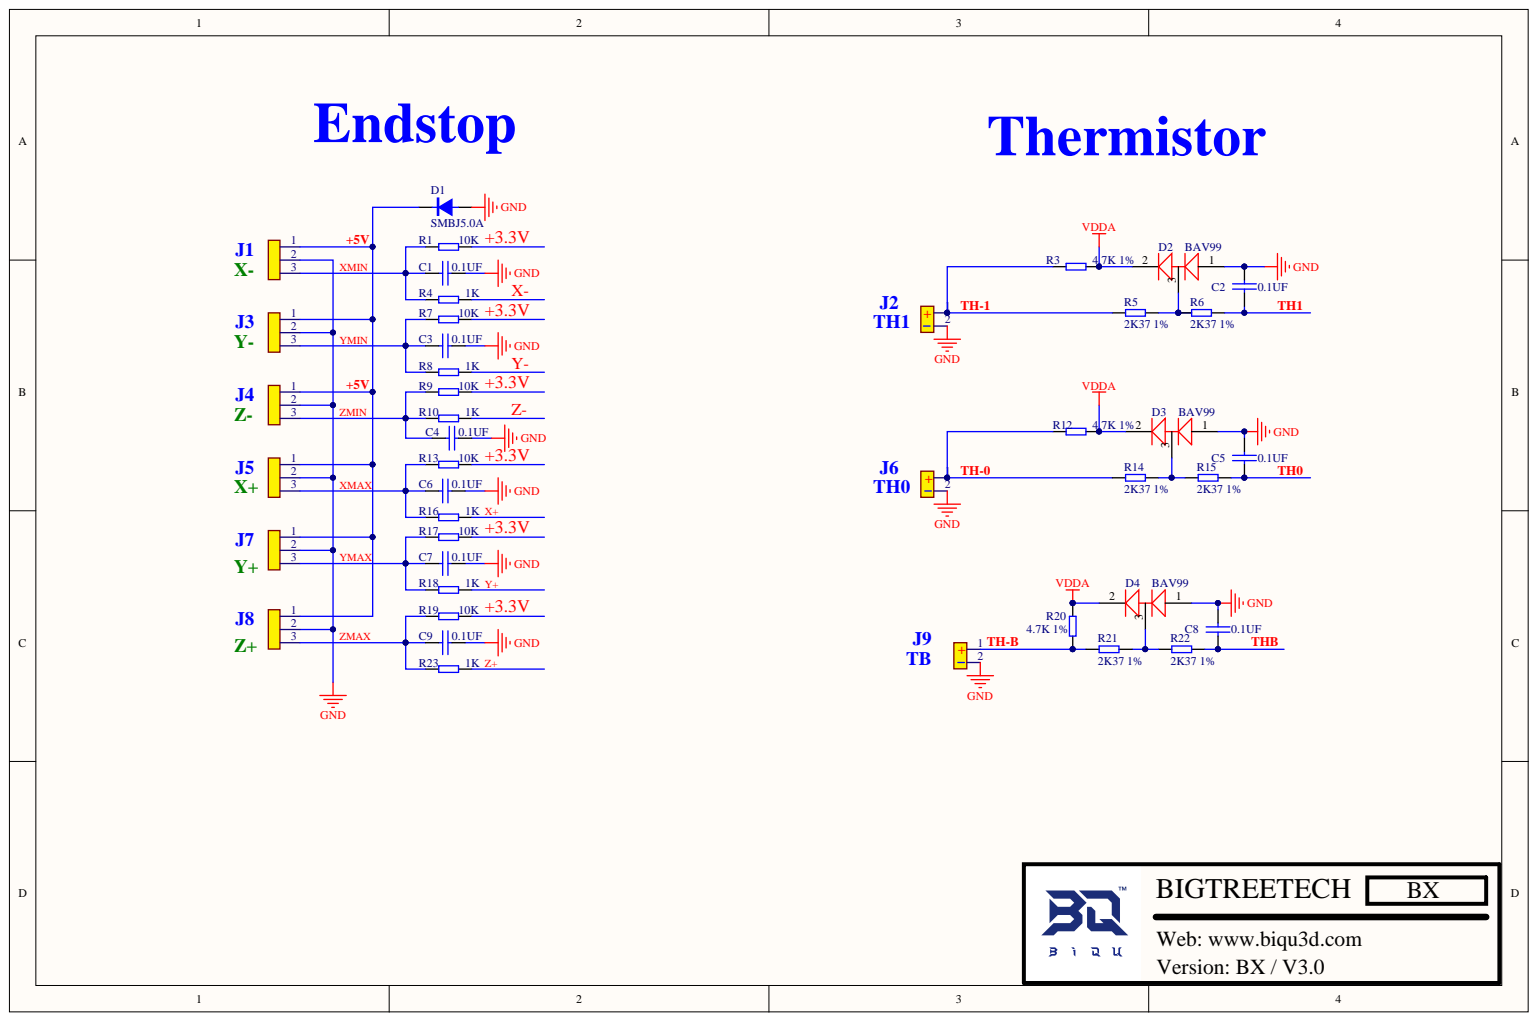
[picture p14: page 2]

123 | | YMIN

123 | | ZMIN

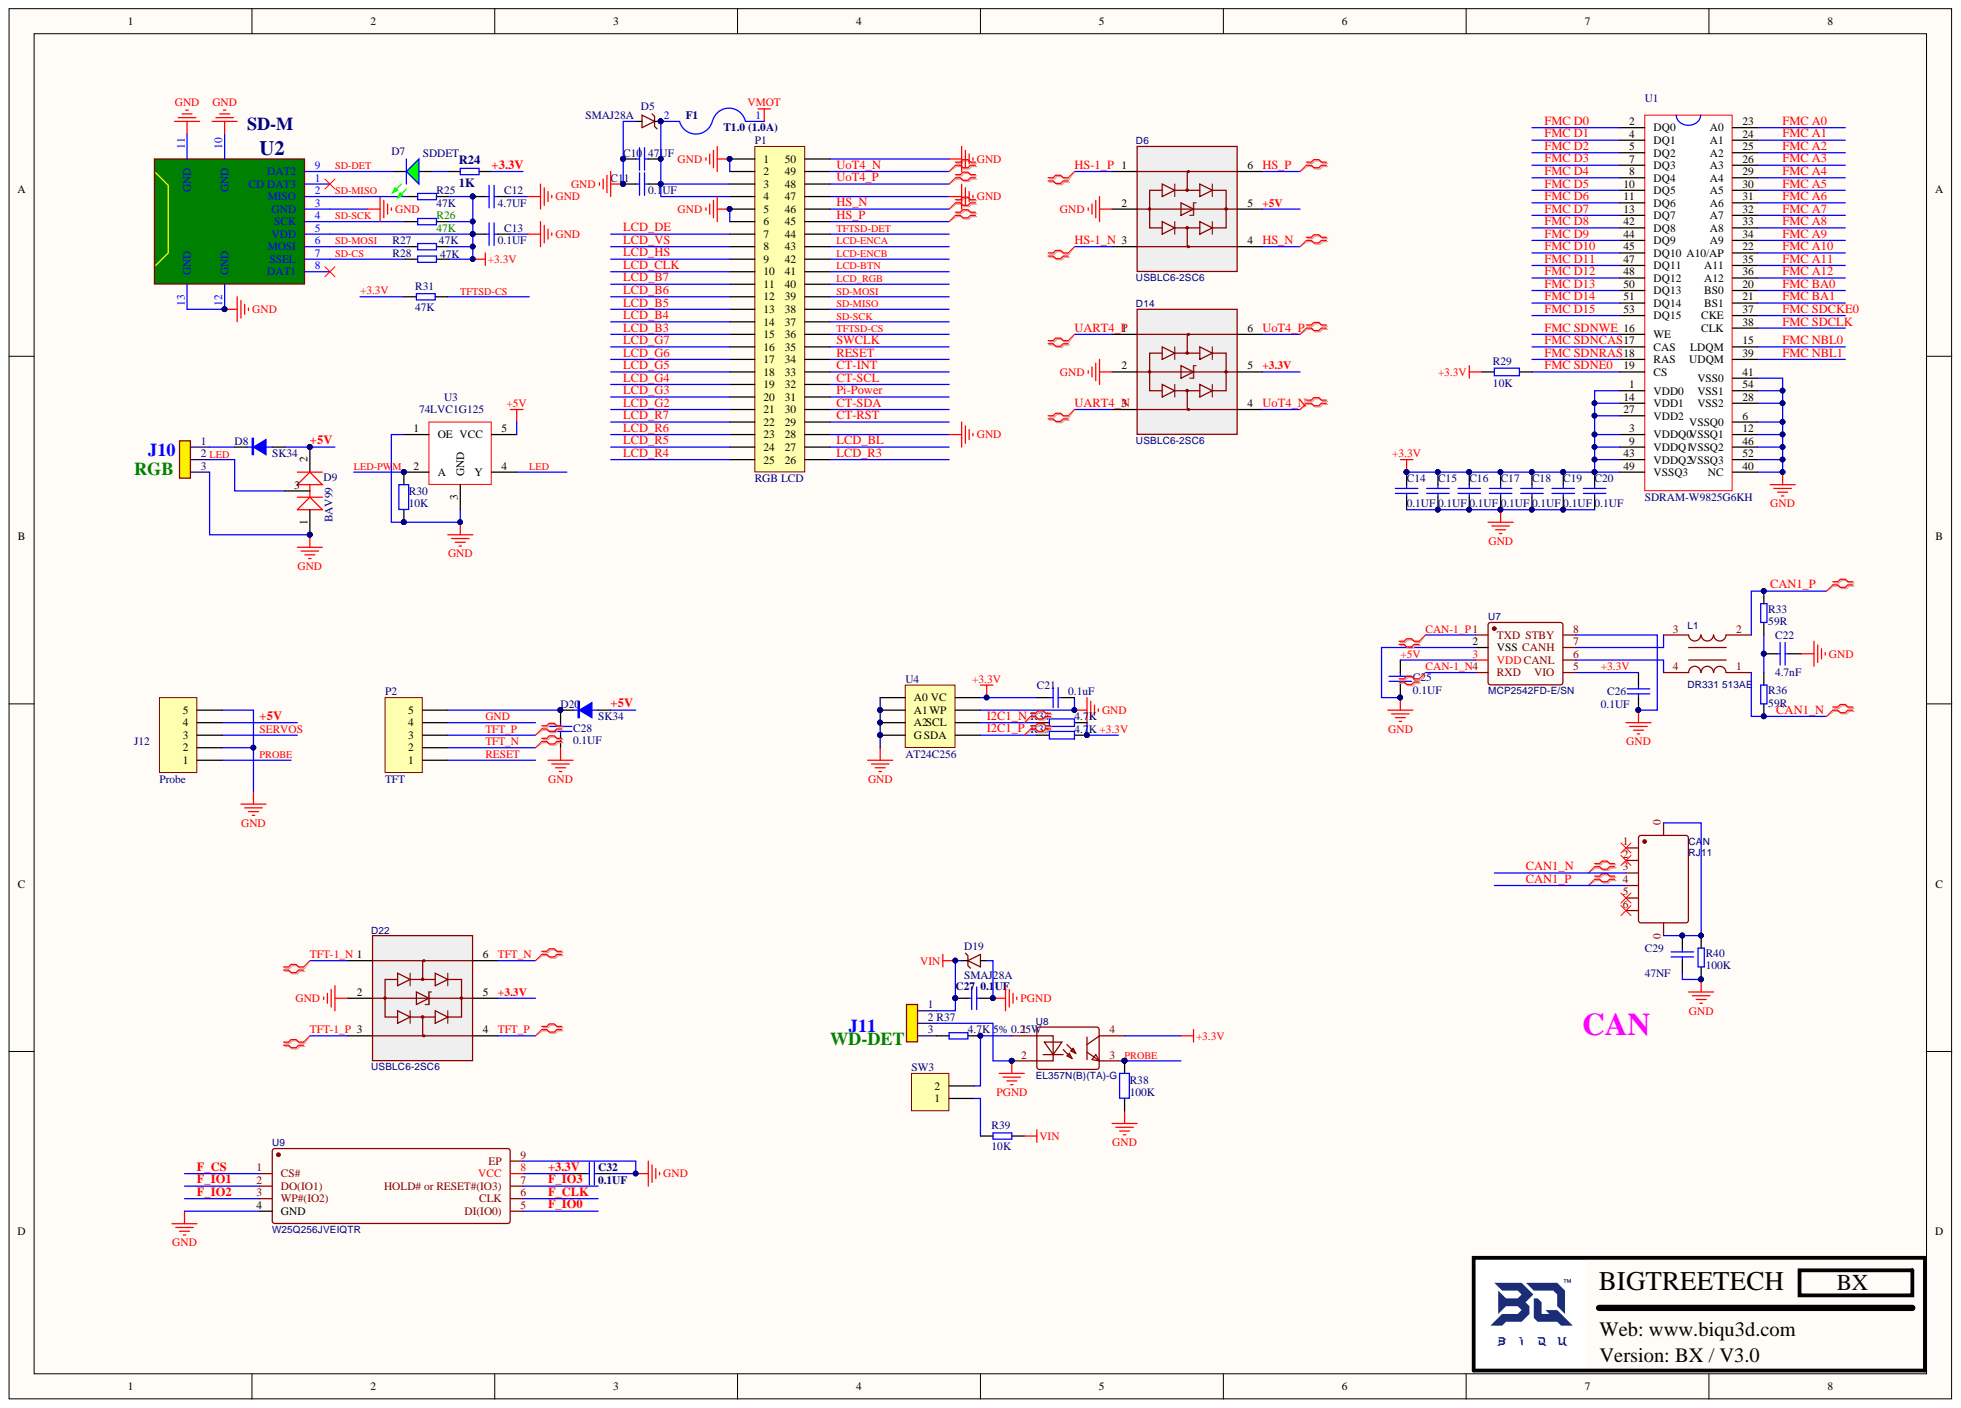
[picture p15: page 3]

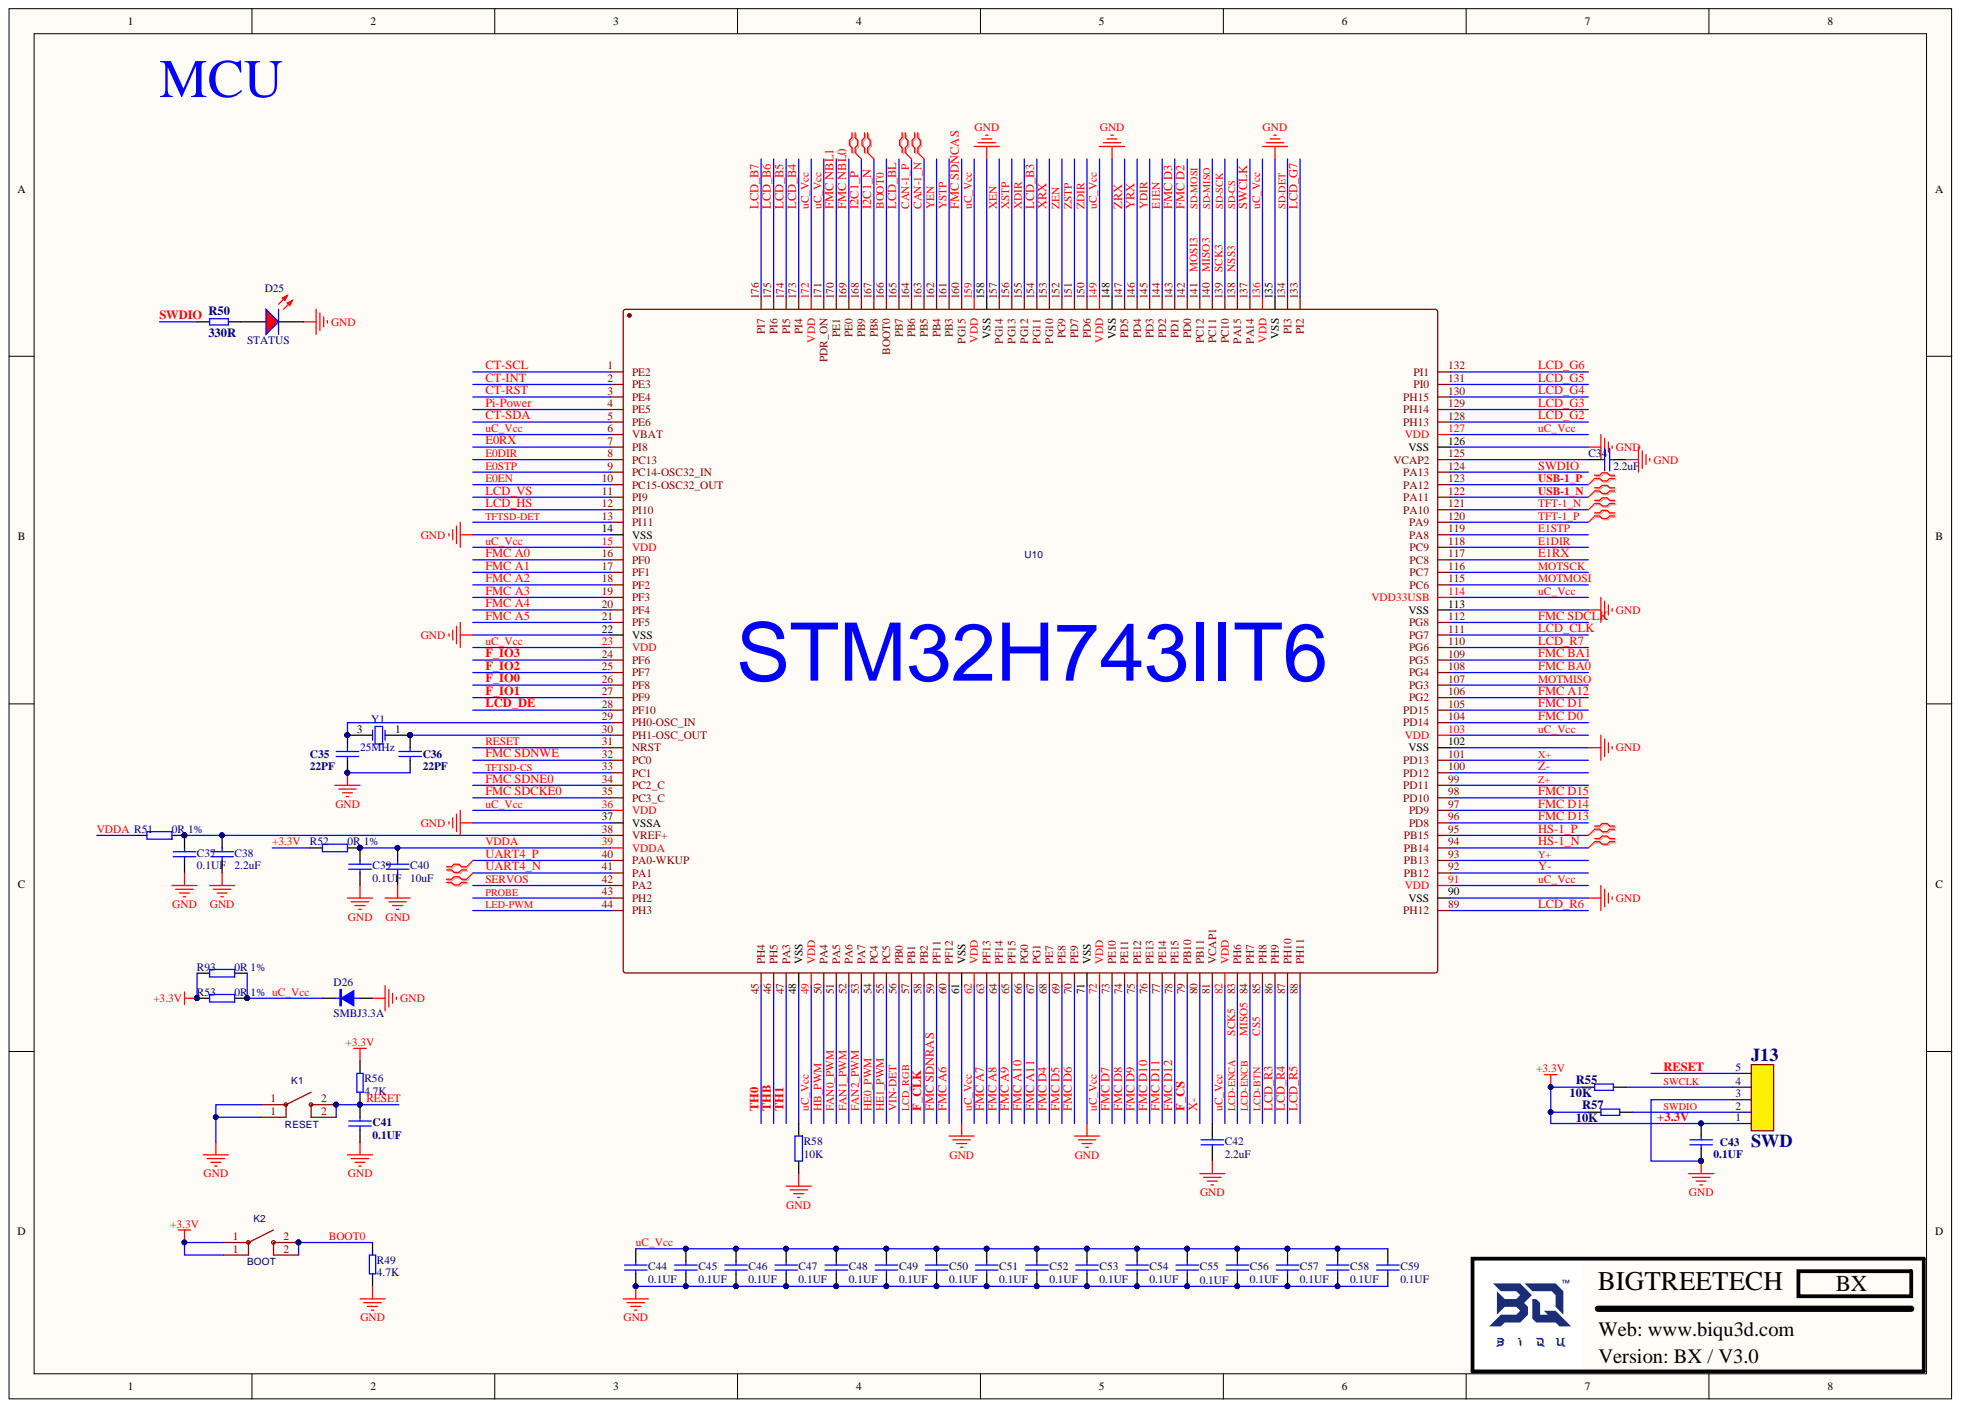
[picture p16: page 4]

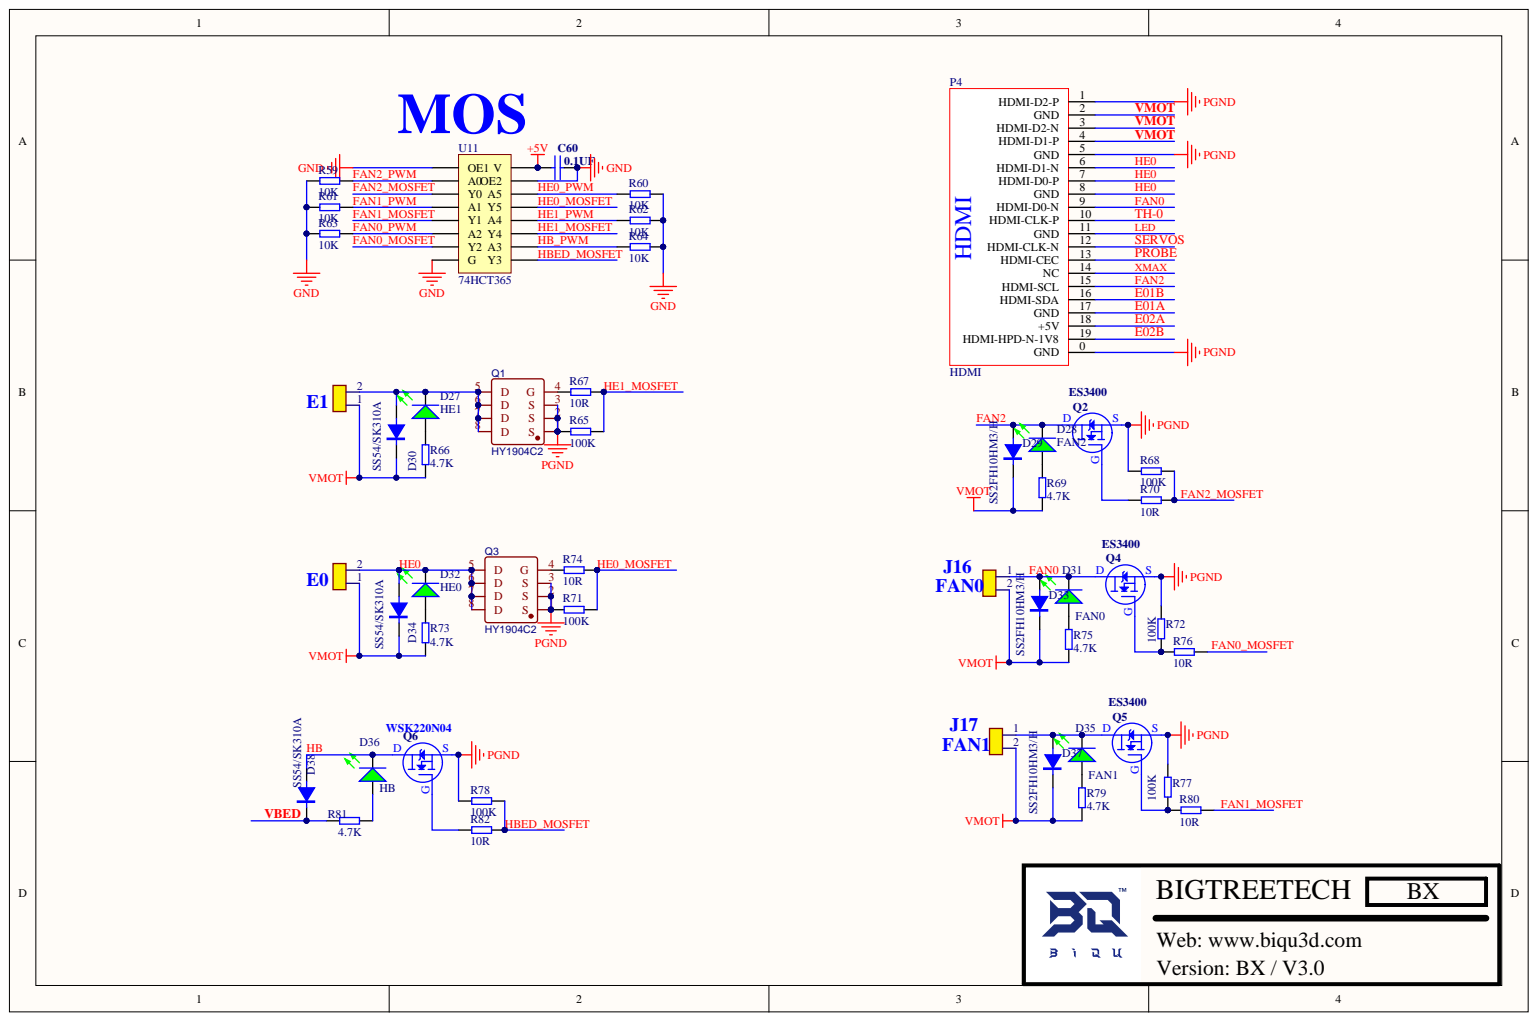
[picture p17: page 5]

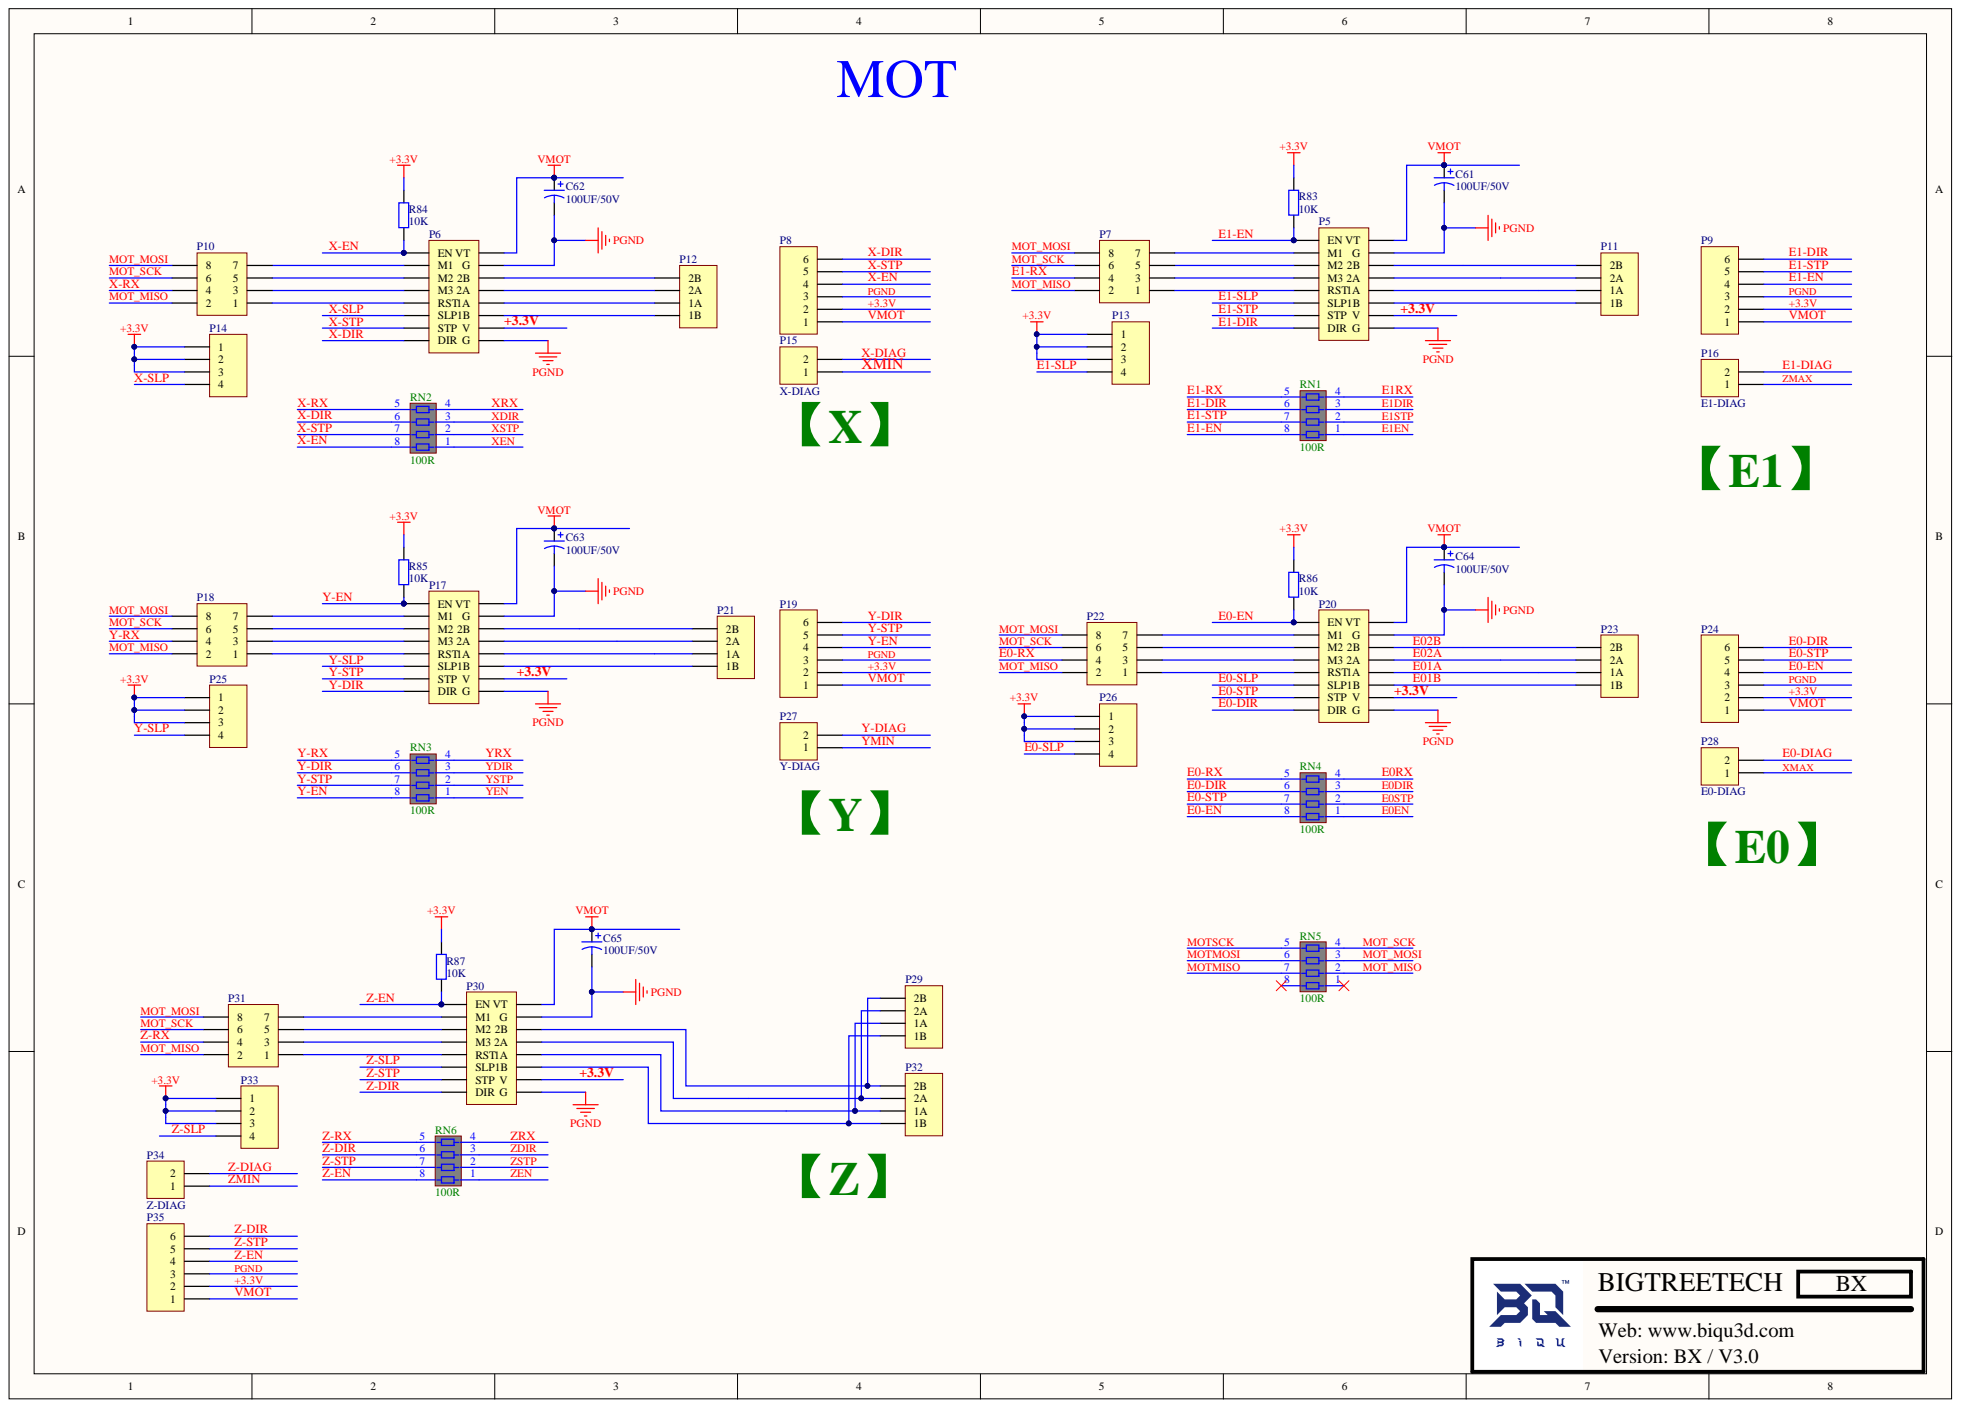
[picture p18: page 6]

1234 | E1-DIR

P32 Z-SLP

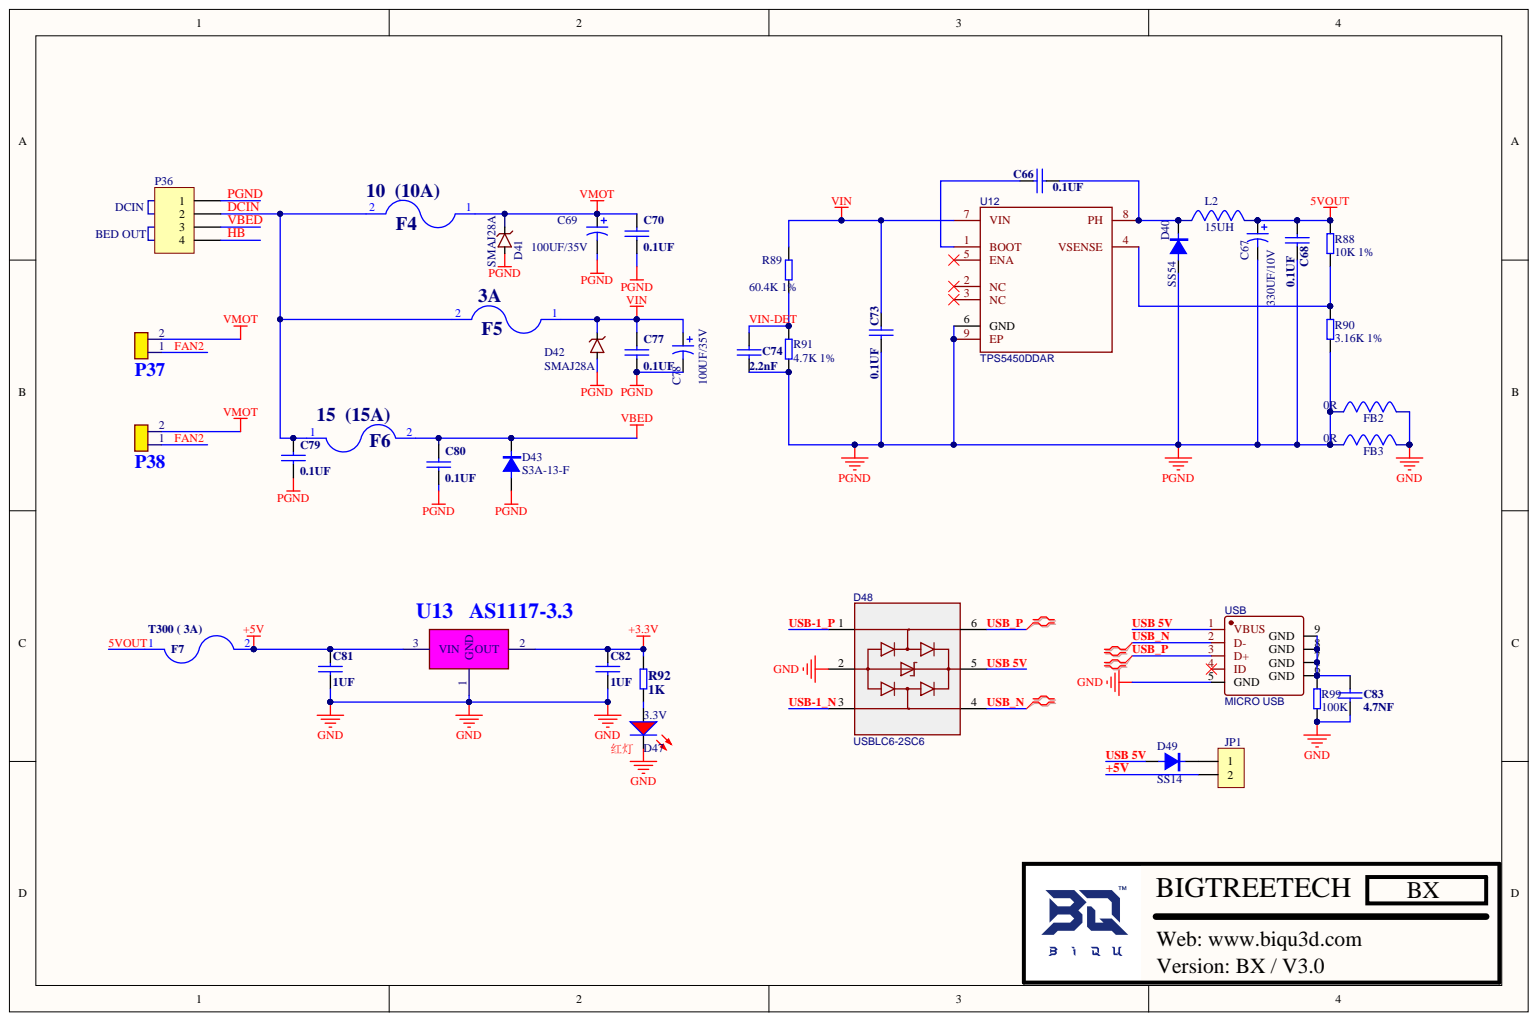
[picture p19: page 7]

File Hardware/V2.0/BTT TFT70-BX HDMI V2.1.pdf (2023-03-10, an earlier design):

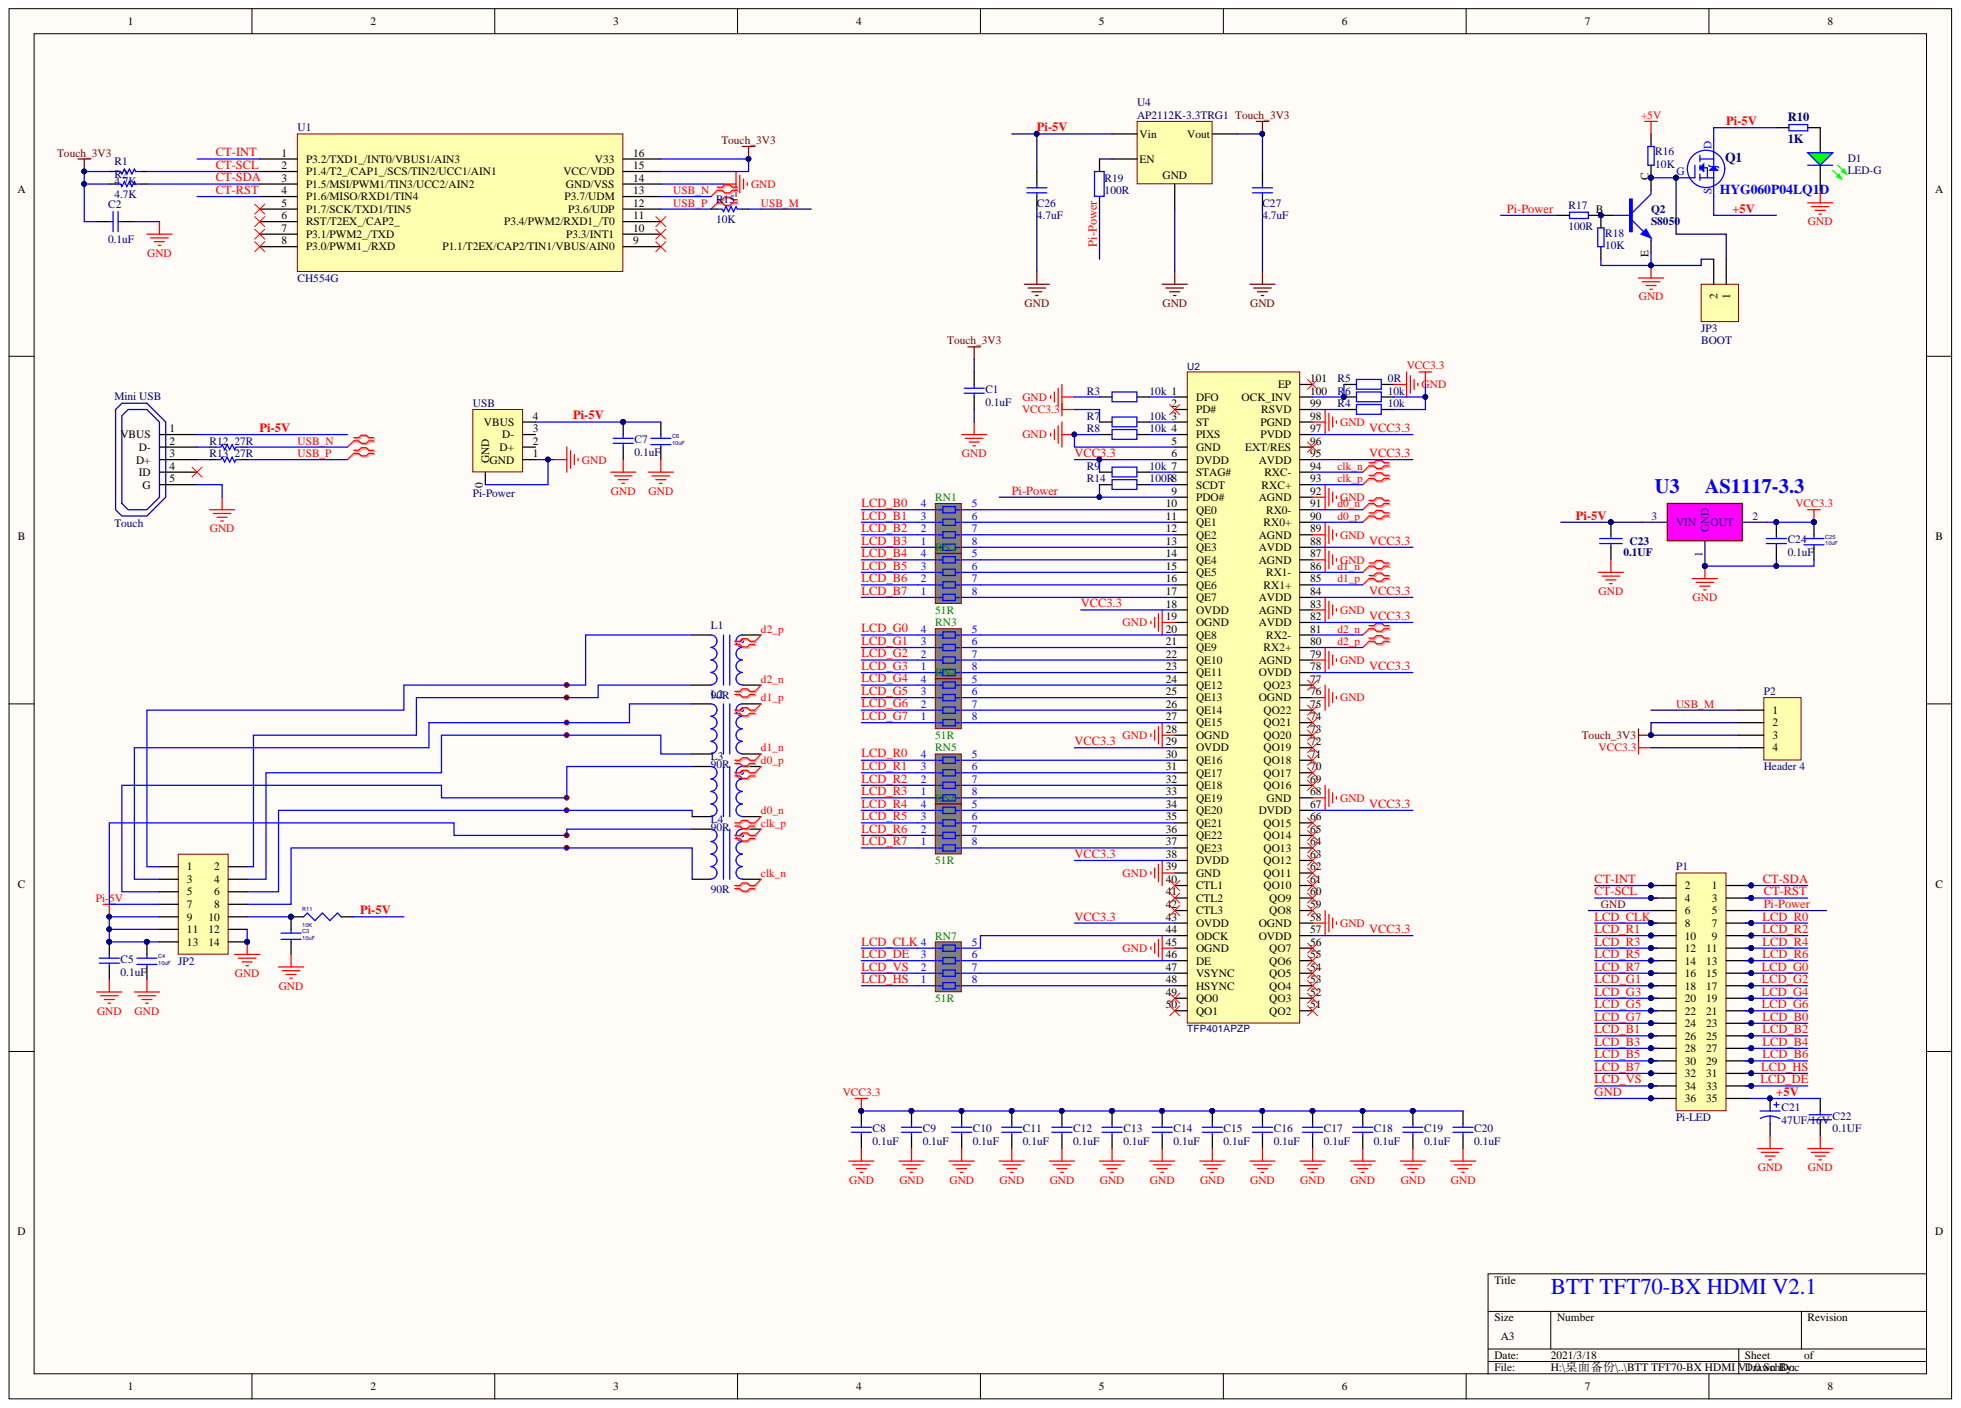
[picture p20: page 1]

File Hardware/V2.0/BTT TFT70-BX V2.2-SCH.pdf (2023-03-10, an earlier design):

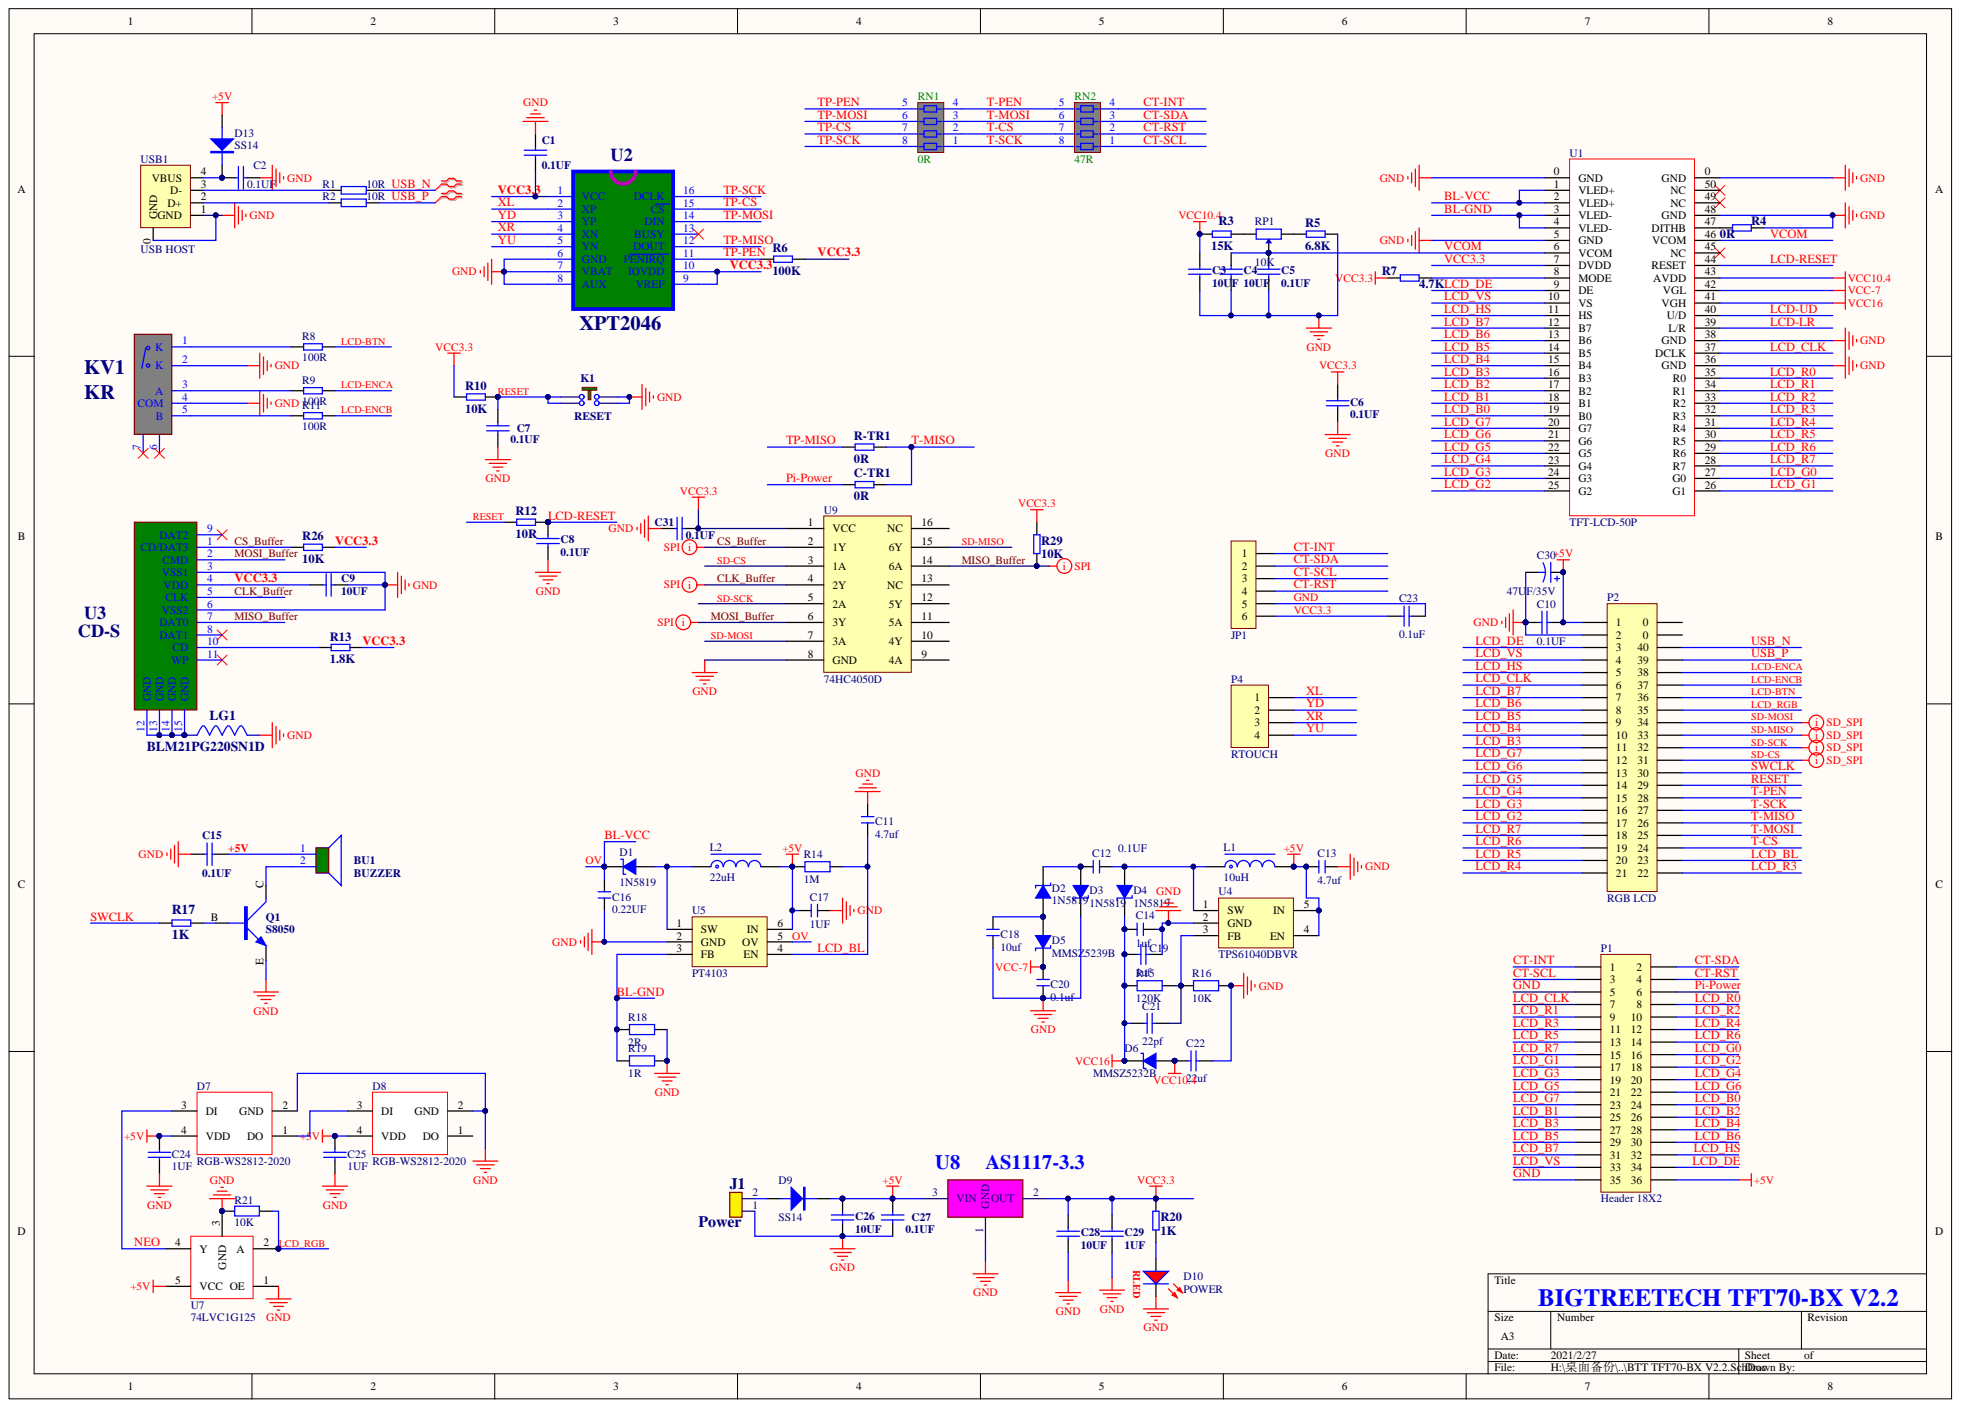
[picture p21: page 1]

TP-CS TP-SCK

CT-SDA CT-INT

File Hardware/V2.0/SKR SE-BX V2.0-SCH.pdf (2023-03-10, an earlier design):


Web: www.biqu3d.com
Version: SKR / SE-BX / V2.0


123 | | YMIN

123 | | ZMIN





P31 Z-SLP


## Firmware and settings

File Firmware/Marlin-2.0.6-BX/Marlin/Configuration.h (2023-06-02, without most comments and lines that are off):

#pragma once
#define CONFIGURATION_H_VERSION 020006
#define STRING_CONFIG_H_AUTHOR "(BIQU, BX)" // Who made the changes.
#define SERIAL_PORT 1
#define SERIAL_PORT_2 -1
#define BAUDRATE 115200
  #define MOTHERBOARD BOARD_BTT_SKR_SE_BX_V1_0
#define CUSTOM_MACHINE_NAME "BIQU-BX"
#define EXTRUDERS 1
#define DEFAULT_NOMINAL_FILAMENT_DIA 1.75
#define TEMP_SENSOR_0 -5
#define TEMP_SENSOR_1 0
#define TEMP_SENSOR_2 0
#define TEMP_SENSOR_3 0
#define TEMP_SENSOR_4 0
#define TEMP_SENSOR_5 0
#define TEMP_SENSOR_6 0
#define TEMP_SENSOR_7 0
#define TEMP_SENSOR_BED 1
#define TEMP_SENSOR_PROBE 0
#define TEMP_SENSOR_CHAMBER 0
#define DUMMY_THERMISTOR_998_VALUE 25
#define DUMMY_THERMISTOR_999_VALUE 100
#define MAX_REDUNDANT_TEMP_SENSOR_DIFF 10
#define TEMP_RESIDENCY_TIME     10  // (seconds) Time to wait for hotend to "settle" in M109
#define TEMP_WINDOW              1  // (°C) Temperature proximity for the "temperature reached" timer
#define TEMP_HYSTERESIS          3  // (°C) Temperature proximity considered "close enough" to the target
#define TEMP_BED_RESIDENCY_TIME 10  // (seconds) Time to wait for bed to "settle" in M190
#define TEMP_BED_WINDOW          1  // (°C) Temperature proximity for the "temperature reached" timer
#define TEMP_BED_HYSTERESIS      3  // (°C) Temperature proximity considered "close enough" to the target
#define HEATER_0_MINTEMP   5
#define HEATER_1_MINTEMP   5
#define HEATER_2_MINTEMP   5
#define HEATER_3_MINTEMP   5
#define HEATER_4_MINTEMP   5
#define HEATER_5_MINTEMP   5
#define HEATER_6_MINTEMP   5
#define HEATER_7_MINTEMP   5
#define BED_MINTEMP        5
#define HEATER_0_MAXTEMP 520
#define HEATER_1_MAXTEMP 275
#define HEATER_2_MAXTEMP 275
#define HEATER_3_MAXTEMP 275
#define HEATER_4_MAXTEMP 275
#define HEATER_5_MAXTEMP 275
#define HEATER_6_MAXTEMP 275
#define HEATER_7_MAXTEMP 275
#define BED_MAXTEMP      150
#define PIDTEMP
#define BANG_MAX 255     // Limits current to nozzle while in bang-bang mode; 255=full current
#define PID_MAX BANG_MAX // Limits current to nozzle while PID is active (see PID_FUNCTIONAL_RANGE below); 255=full current
#define PID_K1 0.95      // Smoothing factor within any PID loop
  #define DEFAULT_Kp 11.89
  #define DEFAULT_Ki 0.40
  #define DEFAULT_Kd 59.08
#define PIDTEMPBED
#define MAX_BED_POWER 255 // limits duty cycle to bed; 255=full current
  #define DEFAULT_bedKp 127.83
  #define DEFAULT_bedKi 20.75
  #define DEFAULT_bedKd 525.0
  #define PID_FUNCTIONAL_RANGE 25 // If the temperature difference between the target temperature and the actual temperature
#define PREVENT_COLD_EXTRUSION
#define EXTRUDE_MINTEMP 170
#define PREVENT_LENGTHY_EXTRUDE
#define EXTRUDE_MAXLENGTH 200
#define THERMAL_PROTECTION_HOTENDS // Enable thermal protection for all extruders
#define THERMAL_PROTECTION_BED     // Enable thermal protection for the heated bed
#define THERMAL_PROTECTION_CHAMBER // Enable thermal protection for the heated chamber
#define USE_XMIN_PLUG
#define USE_YMIN_PLUG
#define USE_ZMIN_PLUG
#define ENDSTOPPULLUPS
#define X_MIN_ENDSTOP_INVERTING false // Set to true to invert the logic of the endstop.
#define Y_MIN_ENDSTOP_INVERTING false // Set to true to invert the logic of the endstop.
#define Z_MIN_ENDSTOP_INVERTING false // Set to true to invert the logic of the endstop.
#define X_MAX_ENDSTOP_INVERTING false // Set to true to invert the logic of the endstop.
#define Y_MAX_ENDSTOP_INVERTING false // Set to true to invert the logic of the endstop.
#define Z_MAX_ENDSTOP_INVERTING false // Set to true to invert the logic of the endstop.
#define Z_MIN_PROBE_ENDSTOP_INVERTING false // Set to true to invert the logic of the probe.
#define X_DRIVER_TYPE  TMC2209
#define Y_DRIVER_TYPE  TMC2209
#define Z_DRIVER_TYPE  TMC2209
#define E0_DRIVER_TYPE TMC2209
#define ENDSTOP_NOISE_THRESHOLD 4
#define ENDSTOP_NOISE_Z
#define DEFAULT_AXIS_STEPS_PER_UNIT   { 80*2, 80*2, 400*2, 932 }
#define DEFAULT_MAX_FEEDRATE          { 200, 200, 5, 40 }
#define DEFAULT_MAX_ACCELERATION      { 1000, 1000, 100, 10000 }
#define DEFAULT_ACCELERATION          800    // X, Y, Z and E acceleration for printing moves
#define DEFAULT_RETRACT_ACCELERATION  800    // E acceleration for retracts
#define DEFAULT_TRAVEL_ACCELERATION   800    // X, Y, Z acceleration for travel (non printing) moves
#define DEFAULT_EJERK    5.0  // May be used by Linear Advance
  #define JUNCTION_DEVIATION_MM 0.013 // (mm) Distance from real junction edge
  #define JD_HANDLE_SMALL_SEGMENTS    // Use curvature estimation instead of just the junction angle
#define S_CURVE_ACCELERATION
#define FIX_MOUNTED_PROBE
#define NOZZLE_TO_PROBE_OFFSET { -30.1, 26.78, 0 }
#define PROBING_MARGIN 30
#define XY_PROBE_SPEED (80*60)
#define Z_PROBE_SPEED_FAST HOMING_FEEDRATE_Z
#define Z_PROBE_SPEED_SLOW (Z_PROBE_SPEED_FAST / 2)
#define Z_CLEARANCE_DEPLOY_PROBE   10 // Z Clearance for Deploy/Stow
#define Z_CLEARANCE_BETWEEN_PROBES  5 // Z Clearance between probe points
#define Z_CLEARANCE_MULTI_PROBE     5 // Z Clearance between multiple probes
#define Z_PROBE_LOW_POINT          -2 // Farthest distance below the trigger-point to go before stopping
#define Z_PROBE_OFFSET_RANGE_MIN -20
#define Z_PROBE_OFFSET_RANGE_MAX 20
#define X_ENABLE_ON 0
#define Y_ENABLE_ON 0
#define Z_ENABLE_ON 0
#define E_ENABLE_ON 0 // For all extruders
#define DISABLE_X false
#define DISABLE_Y false
#define DISABLE_Z false
#define DISABLE_E false             // Disable the extruder when not stepping
#define DISABLE_INACTIVE_EXTRUDER   // Keep only the active extruder enabled
#define INVERT_X_DIR true
#define INVERT_Y_DIR true
#define INVERT_Z_DIR false
#define INVERT_E0_DIR true
#define INVERT_E1_DIR true
#define INVERT_E2_DIR false
#define INVERT_E3_DIR false
#define INVERT_E4_DIR false
#define INVERT_E5_DIR false
#define INVERT_E6_DIR false
#define INVERT_E7_DIR false
#define X_HOME_DIR -1
#define Y_HOME_DIR -1
#define Z_HOME_DIR -1
#define X_BED_SIZE 250
#define Y_BED_SIZE 250
#define X_MIN_POS -12
#define Y_MIN_POS -2
#define Z_MIN_POS 0
#define X_MAX_POS X_BED_SIZE
#define Y_MAX_POS Y_BED_SIZE
#define Z_MAX_POS 250
#define MIN_SOFTWARE_ENDSTOPS
  #define MIN_SOFTWARE_ENDSTOP_X
  #define MIN_SOFTWARE_ENDSTOP_Y
  #define MIN_SOFTWARE_ENDSTOP_Z
#define MAX_SOFTWARE_ENDSTOPS
  #define MAX_SOFTWARE_ENDSTOP_X
  #define MAX_SOFTWARE_ENDSTOP_Y
  #define MAX_SOFTWARE_ENDSTOP_Z
#define AUTO_BED_LEVELING_BILINEAR
#define RESTORE_LEVELING_AFTER_G28
  #define ENABLE_LEVELING_FADE_HEIGHT
  #define SEGMENT_LEVELED_MOVES
  #define LEVELED_SEGMENT_LENGTH 5.0 // (mm) Length of all segments (except the last one)
  #define GRID_MAX_POINTS_X 5
  #define GRID_MAX_POINTS_Y GRID_MAX_POINTS_X
#define HOMING_FEEDRATE_XY (20*60)
#define HOMING_FEEDRATE_Z  (4*60)
#define VALIDATE_HOMING_ENDSTOPS
#define EEPROM_SETTINGS     // Persistent storage with M500 and M501
#define EEPROM_CHITCHAT       // Give feedback on EEPROM commands. Disable to save PROGMEM.
#define EEPROM_BOOT_SILENT    // Keep M503 quiet and only give errors during first load
  #define EEPROM_AUTO_INIT  // Init EEPROM automatically on any errors.
#define HOST_KEEPALIVE_FEATURE        // Disable this if your host doesn't like keepalive messages
#define DEFAULT_KEEPALIVE_INTERVAL 2  // Number of seconds between "busy" messages. Set with M113.
#define BUSY_WHILE_HEATING            // Some hosts require "busy" messages even during heating
#define PREHEAT_1_LABEL       "PLA"
#define PREHEAT_1_TEMP_HOTEND 180
#define PREHEAT_1_TEMP_BED     70
#define PREHEAT_1_FAN_SPEED     0 // Value from 0 to 255
#define PREHEAT_2_LABEL       "ABS"
#define PREHEAT_2_TEMP_HOTEND 240
#define PREHEAT_2_TEMP_BED    110
#define PREHEAT_2_FAN_SPEED     0 // Value from 0 to 255
#define NOZZLE_PARK_FEATURE
  #define NOZZLE_PARK_POINT { (X_MIN_POS + 10), (Y_MAX_POS - 10), 20 }
  #define NOZZLE_PARK_Z_RAISE_MIN   2   // (mm) Always raise Z by at least this distance
  #define NOZZLE_PARK_XY_FEEDRATE 100   // (mm/s) X and Y axes feedrate (also used for delta Z axis)
  #define NOZZLE_PARK_Z_FEEDRATE    5   // (mm/s) Z axis feedrate (not used for delta printers)
#define PRINTJOB_TIMER_AUTOSTART
#define LCD_LANGUAGE en
#define DISPLAY_CHARSET_HD44780 JAPANESE
#define LCD_INFO_SCREEN_STYLE 0
#define SDSUPPORT
#define SPEAKER
#define LCD_FEEDBACK_FREQUENCY_DURATION_MS 20
#define LCD_FEEDBACK_FREQUENCY_HZ 1000
#define BTT_STYLE_UI
#define EXTENSIBLE_UI
  #define EXTUI_LOCAL_BEEPER // Enables use of local Beeper pin with external display
#define TFT_1024x600_LTDC
#define SOFT_PWM_SCALE 0
#define NEOPIXEL_LED
  #define NEOPIXEL_TYPE   NEO_GRB // NEO_GRBW / NEO_GRB - four/three channel driver type (defined in Adafruit_NeoPixel.h)
  #define NEOPIXEL2_TYPE NEOPIXEL_TYPE
  #define NEOPIXEL_PIXELS 15       // Number of LEDs in the strip. (Longest strip when NEOPIXEL2_SEPARATE is disabled.)
  #define NEOPIXEL_IS_SEQUENTIAL   // Sequential display for temperature change - LED by LED. Disable to change all LEDs at once.
  #define NEOPIXEL_BRIGHTNESS 127  // Initial brightness (0-255)
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

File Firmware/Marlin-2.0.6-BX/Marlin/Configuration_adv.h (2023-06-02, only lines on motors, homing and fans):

#define E0_AUTO_FAN_PIN PA7
#define E1_AUTO_FAN_PIN -1
#define E2_AUTO_FAN_PIN -1
#define E3_AUTO_FAN_PIN -1
#define E4_AUTO_FAN_PIN -1
#define E5_AUTO_FAN_PIN -1
#define E6_AUTO_FAN_PIN -1
#define E7_AUTO_FAN_PIN -1
#define CHAMBER_AUTO_FAN_PIN -1
#define HOMING_BUMP_MM      { 0, 0, 2 }       // (mm) Backoff from endstops after first bump
#define HOMING_BUMP_DIVISOR { 2, 2, 4 }       // Re-Bump Speed Divisor (Divides the Homing Feedrate)
#define HOMING_BACKOFF_POST_MM { 5, 5, 2 }  // (mm) Backoff from endstops after homing
#define MICROSTEP_MODES { 16, 16, 16, 16, 16, 16 } // [1,2,4,8,16]
  #define BABYSTEP_WITHOUT_HOMING
#define LIN_ADVANCE
  #define LIN_ADVANCE_K 0    // Unit: mm compression per 1mm/s extruder speed
#define ADVANCED_PAUSE_FEATURE
  #define ADVANCED_PAUSE_PURGE_FEEDRATE        6  // (mm/s) Extrude feedrate (after loading). Should be slower than load feedrate.
  #define ADVANCED_PAUSE_PURGE_LENGTH         10  // (mm) Length to extrude after loading.
  #define ADVANCED_PAUSE_RESUME_PRIME          0  // (mm) Extra distance to prime nozzle after returning from park.
  #define HOME_BEFORE_FILAMENT_CHANGE           // If needed, home before parking for filament change
    #define X_CURRENT       1050        // (mA) RMS current. Multiply by 1.414 for peak current.
    #define X_CURRENT_HOME  (350)  // (mA) RMS current for sensorless homing
    #define X_MICROSTEPS     16    // 0..256
    #define Y_CURRENT       1050
    #define Y_CURRENT_HOME  (400)
    #define Y_MICROSTEPS     16
    #define Z_CURRENT       1050
    #define Z_CURRENT_HOME  Z_CURRENT
    #define Z_MICROSTEPS     16
    #define E0_CURRENT      1050
    #define E0_MICROSTEPS    16
  #define X_HYBRID_THRESHOLD     100  // [mm/s]
  #define X2_HYBRID_THRESHOLD    100
  #define Y_HYBRID_THRESHOLD     100
  #define Y2_HYBRID_THRESHOLD    100
  #define Z_HYBRID_THRESHOLD       3
  #define Z2_HYBRID_THRESHOLD      3
  #define Z3_HYBRID_THRESHOLD      3
  #define Z4_HYBRID_THRESHOLD      3
  #define E0_HYBRID_THRESHOLD     30
  #define E1_HYBRID_THRESHOLD     30
  #define E2_HYBRID_THRESHOLD     30
  #define E3_HYBRID_THRESHOLD     30
  #define E4_HYBRID_THRESHOLD     30
  #define E5_HYBRID_THRESHOLD     30
  #define E6_HYBRID_THRESHOLD     30
  #define E7_HYBRID_THRESHOLD     30
  #define SENSORLESS_HOMING // StallGuard capable drivers only
    #define X_STALL_SENSITIVITY  100
    #define X2_STALL_SENSITIVITY X_STALL_SENSITIVITY
    #define Y_STALL_SENSITIVITY  100
    #define Y2_STALL_SENSITIVITY Y_STALL_SENSITIVITY
    #define IMPROVE_HOMING_RELIABILITY

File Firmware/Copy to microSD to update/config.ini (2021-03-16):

#### Default Config file for BigTreeTech TFT Controllers
#
# BIGTREE_TFT35_V1_1 / BIGTREE_TFT35_V1_2    / BIGTREE_TFT35_V2_0
# BIGTREE_TFT35_V3_0 / BIGTREE_TFT35_E3_V3_0 / BIGTREE_TFT28_V1_0
# BIGTREE_TFT28_V3_0 / BIGTREE_TFT24_V1_1    / MKS_32_V1_4
#
# Firmware Source: https://github.com/bigtreetech/BIGTREETECH-TouchScreenFirmware


#--------------------------------------------------------------------
# Supported Marlin Firmware Version
#--------------------------------------------------------------------
#  Minimum Marlin Firmware Version: Bugfix-2.0.x
#  Distribution date: 2020-05-12
#  Source: https://github.com/MarlinFirmware/Marlin/tree/bugfix-2.0.x


#--------------------------------------------------------------------
# General Settings
#--------------------------------------------------------------------

#### UNIFIED MENU / CLASSIC MENU
# Select a UI Menu flavour
# Options: [Unified Menu: 1, Classic Menu: 0]
unified_menu:1

#### Baudrate
# Options: [2400: 0, 9600: 1, 19200: 2, 38400: 3, 57600: 4, 115200: 5, 250000: 6, 500000: 7, 1000000: 8]
baudrate:5

#### Default Touch Mode Language
# Select the language to display on the LCD while in Touch Mode.
# Options: [ENGLISH: 0,  CHINESE: 1,     RUSSIAN: 2,  JAPANESE: 3,    ARMENIAN: 4,
#            GERMAN: 5,    CZECH: 6,       SPAIN: 7,    FRENCH: 8,  PORTUGUESE: 9,
#           ITALIAN: 10,  POLISH: 11,     SLOVAK: 12,    DUTCH: 13,  HUNGARIAN: 14,
#           TURKISH: 15,   GREEK: 16,  SLOVENIAN: 17,  CATALAN: 18]
language:0

#### Default Touch Mode Color Options
# Options: [ WHITE: 0,  BLACK: 1,  RED: 2,  GREEN: 3,      BLUE: 4,       CYAN: 5,  MAGENTA: 6,    YELLOW: 7,
#           ORANGE: 8, PURPLE: 9, LIME: 10, BROWN: 11, DARKBLUE: 12, DARKGREEN: 13,    GRAY: 14, DARKGRAY: 15]
# Or set the color(RGB888 format) hex value directly(start with “0x”).
# Such as: 0xFF0000 : Red, 0x00FF00 : Green, 0x0000FF : Blue
# Title background color
title_back_color:1

# Background color
background_color:1

# Font foreground color
font_color:0

# Reminder font color, such as: "No print attached", "Busy processing", etc.
reminder_color:2

# Volume status/reminder font color, such as: "Card inserted", "Card removed"
volume_status_color:5

# Backgroud color for X Y Z position display in Status Screen.
status_xyz_bg_color:15

# List View Border Color
list_border_color:15

# List View button background color
list_button_bg_color:15

#### Rotate UI 180 degrees
# Options: [enable: 1, disable: 0]
rotate_ui:1

#### Show or hide Temperature ACK in Gcode Terminal
# Options: [Show: 1, Hide: 0]
terminal_ack:0

#### invert X axis button function in Move menu to match move buttons to actual axis
# Options: [enable: 1, disable: 0]
# Invert Axis format      [ X<option> Y<option> Z<option> E<option>]
invert_axis:X0 Y0 Z0

#### Persistent temperature info
# show persistent temperature info on all menu screens
# Options: [enable: 1, disable: 0]
persistent_info:1

#### File List Mode
# show file as list
# Options: [enable: 1, disable: 0]
files_list_mode:0

#### Notification style for ACK messages
# Set the notification style to use for displaying the ACK messages which start with 'echo:'
#
# NOTE: The OFF value is applied to any ACK message type (e.g. even to known echo ACK).
#       It means that any kind of ACK message is silently discard
#
# Options: [OFF: 0, POPUP: 1, TOAST: 2]
#   OFF:   No notification. The message is ignored.
#   POPUP: Display a popup window for user confirmation.
#   TOAST: A non-blocking Toast notification is displayed for few seconds. No user interaction is needed
ack_notification:1

#--------------------------------------------------------------------
# Marlin Mode Settings (Only for TFT24_V1.1 & TFT28/TFT35/TFT43/TFT50/TFT70_V3.0)
#--------------------------------------------------------------------

#### Default Mode
# Options: [0: Marlin Mode, 1: Touch Mode]
default_mode:1

#### Keep Serial Always ON
# Keep UART (Serial communication) alive in Marlin Mode
# Allow seamless OctoPrint UART connection to the TFT's UART/serial expansion port no matter which mode the TFT is in.
# Options: [0: Disabled, 1: Enabled]
serial_always_on:0

#### Default Marlin Mode Background & Font Color Options
# Options: [ WHITE: 0,  BLACK: 1,  RED: 2,  GREEN: 3,      BLUE: 4,       CYAN: 5,  MAGENTA: 6,    YELLOW: 7,
#           ORANGE: 8, PURPLE: 9, LIME: 10, BROWN: 11, DARKBLUE: 12, DARKGREEN: 13,    GRAY: 14, DARKGRAY: 15]
# Or set the color(RGB888 format) hex value directly(start with “0x”).
# Such as: 0xFF0000 : Red, 0x00FF00 : Green, 0x0000FF : Blue
marlin_bg_color:1
marlin_fn_color:8

#### Marlin Mode show title
# Options: [enable: 1, disable: 0]
marlin_show_title:1

# Run Marlin Mode in Fullscreen
# Options: [enable: 1, disable: 0] [Disabled. RECOMMENDED FOR TFT24]
marlin_fullscreen:0

# Select marlin type
# Options: [LCD12864: 1, LCD2004: 0]
marlin_type:1

#### Text displayed at the top of the TFT in Marlin Mode.
marlin_title:LCD12864 Simulator
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

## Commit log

2021-02-02 set E0_AUTO_FAN instead of CONTROLLER_FAN
    [Configuration_adv.h]
2021-03-16 update misc
    [Configuration.h, Configuration_adv.h]
2021-03-16 ServoPin_t problem limit pinNum <= 63, set PA2 = 62 fix Bltouch problem
2021-03-29 Add Parts Cooling Fan STL (#6)
    Imported original from SD card.
    [Parts-Cooling-Fan.stl]
2021-06-29 Add Drawer STL (#13)
    [Drawer.stl]
2021-11-11 open source materials
2022-03-12 don't read spi flash id
2023-06-02 update dsi driver to lastest kernel 6.1.21
    [Configuration.h, Configuration_adv.h]

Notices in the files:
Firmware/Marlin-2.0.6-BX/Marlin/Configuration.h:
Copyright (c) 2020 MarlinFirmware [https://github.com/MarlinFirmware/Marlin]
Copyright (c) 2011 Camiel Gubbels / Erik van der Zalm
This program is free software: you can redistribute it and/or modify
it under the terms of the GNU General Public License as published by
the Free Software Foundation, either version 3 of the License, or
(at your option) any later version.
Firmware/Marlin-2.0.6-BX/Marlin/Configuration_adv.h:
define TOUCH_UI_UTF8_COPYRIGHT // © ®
